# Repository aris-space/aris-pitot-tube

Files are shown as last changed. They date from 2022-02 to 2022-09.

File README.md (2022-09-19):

# ARIS Pitot Tube 

This pitot tube prototype is designed as an all-in-one plug-and-play system to gather data.  
<p align="center">
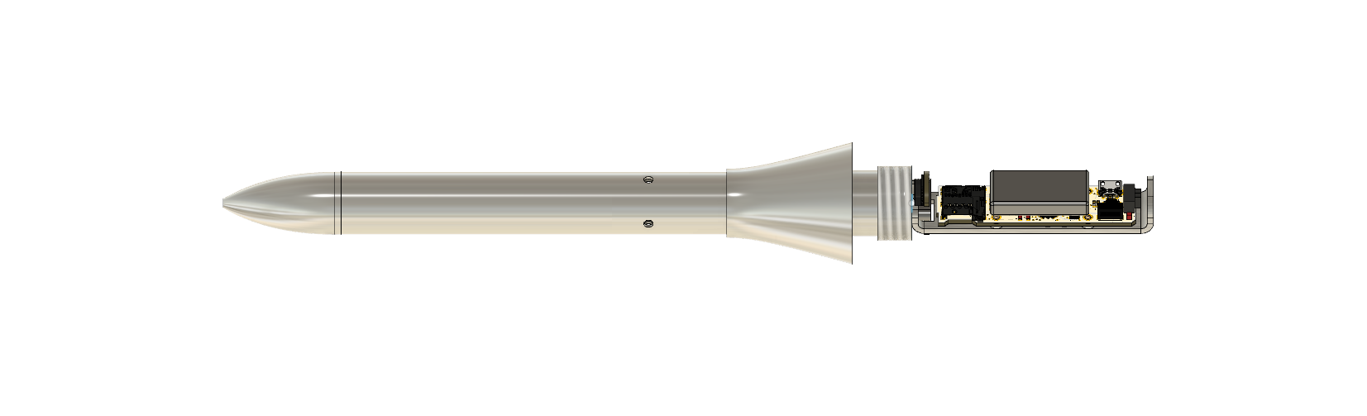
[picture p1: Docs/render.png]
  
</p>
The controller is based on an STM32F405 and mounted directly to the tube along with two MS5803 barometers, one MCP9600 thermocouple ADC, one ICM20601 accelerometer, an SD card and a battery.  
The software uses freeRTOS and will put the MCU in standby mode until the IMU wakes it up during lift-off (interrupt out of IMU to wakeup pin 1 on MCU).  
Preliminary measurements show that the current consumption in flight mode is 150mA and in sleep mode 3mA. With a 240mAh battery, this allows for 80h of sleep time or 1.6h of flight time.  

Below is a diagram explaining the software architecture.  
<p align="center">
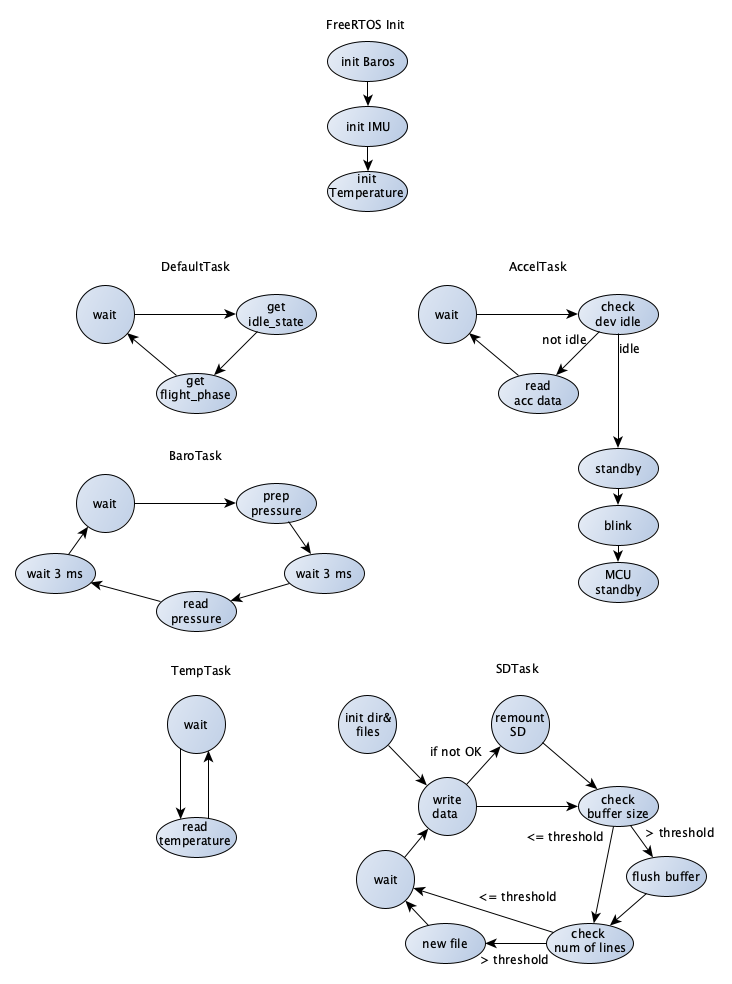
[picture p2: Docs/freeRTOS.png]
  
</p>
  
Repo structure:  
`Hardware` contains all step files and technical drawings to manufacture and assemble the structural components as well as the EAGLE files of the electronics hardware  
`Core/Inc` contains headers of project specific code  
`Core/Src` contains source of project specific code  
`Python` contains python code for analysis (including supersonic flight data from SPAC2022, HELVETIA)  
<p align="center">
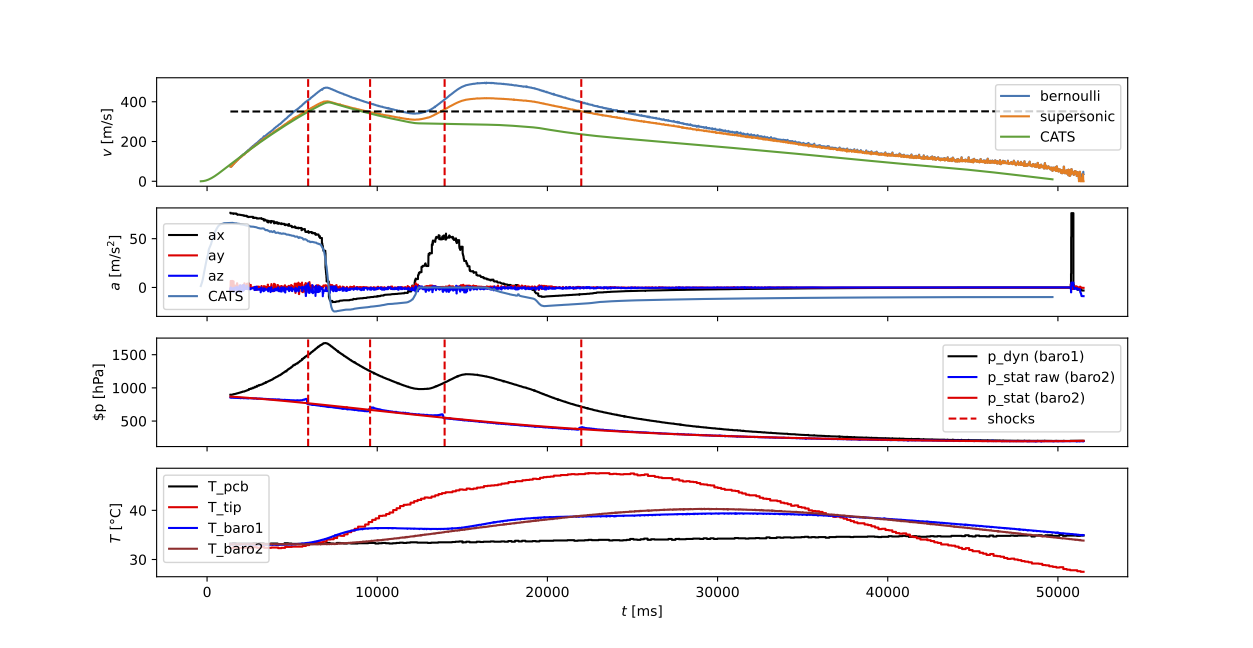
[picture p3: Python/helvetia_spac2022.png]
  
</p>

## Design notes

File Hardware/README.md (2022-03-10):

The CAD with step files and technical drawings can be found in the `CAD` folder.  
`PCB/PitotCTRLBoard` is the controller PCB with the MCU, IMU, ADC and SD-card on it  
`PCB/PitotPBoard3` is the sensor board containing the two Barometers  
The two boards are connected with 3V3, GND, and two I2C lines.  
Consult the `BOM.csv` to order the components, and `assembly_instructions.txt` to mount the hardware.  
`TODO.txt` contains a list of possible improvoments for future interations
<p align="center">
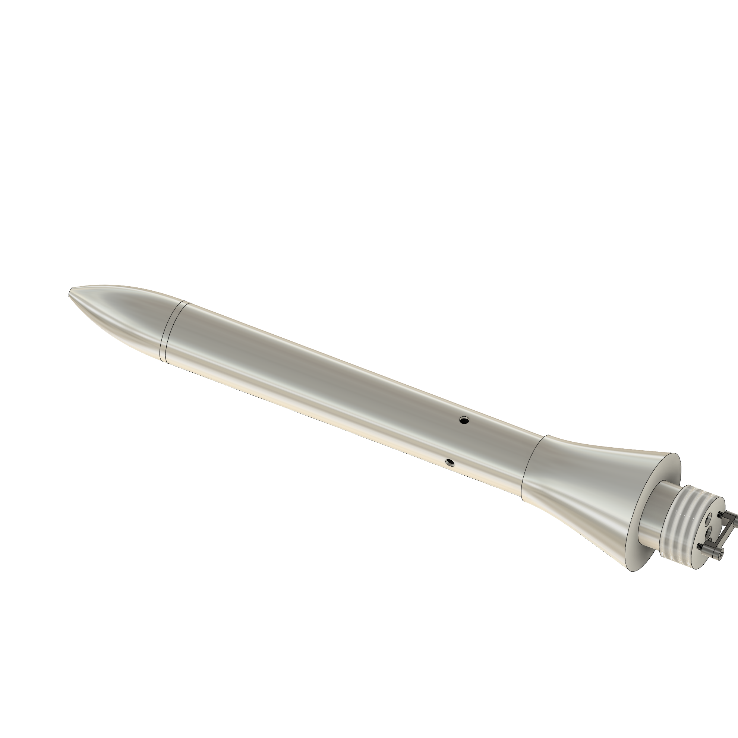
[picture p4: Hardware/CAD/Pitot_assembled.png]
  
</p>

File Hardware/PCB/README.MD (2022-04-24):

`PitotCTRLboard2` is the old control board with micro USB and custom debug connector  

`PitotCTRLboard3` is the new control board with USB-C and Tag-Connect debug connector (PCB is slightly longer)  

`PitotPboard3` is the sensor board, where the barometers are mounted

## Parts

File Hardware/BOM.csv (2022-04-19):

Qty | Value | Device | Package | Parts | Description | ALLIED_NUMBER | ALLIED_PRICE-STOCK | ARROW_PART_NUMBER | ARROW_PRICE-STOCK | AVAILABILITY | CUI_PURCHASE_URL | DESCRIPTION | DIGIKEY-PURCHASE-URL | HEIGHT | MANUFACTURER | MANUFACTURER_NAME | MANUFACTURER_PART_NUMBER | MF | MOUSER-PURCHASE-URL | MOUSER_PART_NUMBER | MOUSER_PRICE-STOCK | MP | PACKAGE | PARTREV | PRICE | RS_PART_NUMBER | RS_PRICE-STOCK | SPICEPREFIX | STANDARD
3 |  | LEDCHIPLED_0805 | CHIPLED_0805 | CHRG / RDY / STAT | LED
12 | 0.1uF | C-EUC0603K | C0603K | C1 / C2 / C3 / C37 | CAPACITOR / European symbol |  |  |  |  |  |  |  |  |  |  |  |  |  |  |  |  |  |  |  |  |  |  | C
1 | 0.47uF | C-EUC0603K | C0603K | C5 | CAPACITOR / European symbol |  |  |  |  |  |  |  |  |  |  |  |  |  |  |  |  |  |  |  |  |  |  | C
6 | 10k | R-EU_R0603 | R0603 | R6 / R7 / R8 / R9 / R12 / R36 | RESISTOR / European symbol |  |  |  |  |  |  |  |  |  |  |  |  |  |  |  |  |  |  |  |  |  |  | R
2 | 15pF | C-EUC0603K | C0603K | C16 / C17 | CAPACITOR / European symbol |  |  |  |  |  |  |  |  |  |  |  |  |  |  |  |  |  |  |  |  |  |  | C
2 | 1k | R-EU_R0603 | R0603 | R43 / R45 | RESISTOR / European symbol |  |  |  |  |  |  |  |  |  |  |  |  |  |  |  |  |  |  |  |  |  |  | R
2 | 1uF | C-EUC0603K | C0603K | C14 / C15 | CAPACITOR / European symbol |  |  |  |  |  |  |  |  |  |  |  |  |  |  |  |  |  |  |  |  |  |  | C
3 | 2.2uF | C-EUC0603K | C0603K | C4 / C11 / C12 | CAPACITOR / European symbol |  |  |  |  |  |  |  |  |  |  |  |  |  |  |  |  |  |  |  |  |  |  | C
1 | 2201778-1 | 2201778-1 | TE_2201778-1 | J1 | MICRO SD PUSH PUSH LOW PROFILE TYPE |  |  |  |  |  |  |  |  |  | TE Connectivity |  |  |  |  |  |  |  |  | B |  |  |  |  | Manufacturer recommendations
1 | 2k | R-EU_R0603 | R0603 | R10 | RESISTOR / European symbol |  |  |  |  |  |  |  |  |  |  |  |  |  |  |  |  |  |  |  |  |  |  | R
1 | 2k2 | R-EU_R0603 | R0603 | R11 | RESISTOR / European symbol |  |  |  |  |  |  |  |  |  |  |  |  |  |  |  |  |  |  |  |  |  |  | R
1 | 330uF | T491C106K035AT | CAPPM6032X280N | C13 | KEMET 10uF 35V dc Tantalum Capacitor MnO2 Solid +/-10% Tolerance T491 Series | 70610893 | https://www.alliedelec.com/kemet-t491c106k035at/70610893/ |  |  |  |  | KEMET 10uF 35V dc Tantalum Capacitor MnO2 Solid +/-10% Tolerance T491 Series |  | 2.8mm |  | Kemet | T491C106K035AT |  |  | 80-T491C106K035 | https://www.mouser.com/Search/Refine.aspx?Keyword=80-T491C106K035 |  |  |  |  | 8015520 | https://uk.rs-online.com/web/p/products/8015520
1 | 3k3 | R-EU_R0603 | R0603 | R13 | RESISTOR / European symbol |  |  |  |  |  |  |  |  |  |  |  |  |  |  |  |  |  |  |  |  |  |  | R
1 | 470 | R-EU_R0603 | R0603 | R14 | RESISTOR / European symbol |  |  |  |  |  |  |  |  |  |  |  |  |  |  |  |  |  |  |  |  |  |  | R
6 | 47k | R-EU_R0603 | R0603 | R1 / R2 / R3 / R4 / R5 / R26 | RESISTOR / European symbol |  |  |  |  |  |  |  |  |  |  |  |  |  |  |  |  |  |  |  |  |  |  | R
1 | ABM8AIG-8.000MHZ-1Z-T | ABM8AIG-8.000MHZ-1Z-T | ABM8AIG8000MHZ1ZT | CLOCK | Crystals 18pF 8MHz 10ppm AEC-Q200 -40C +125C |  |  |  |  |  |  | Crystals 18pF 8MHz 10ppm AEC-Q200 -40C +125C |  | 0.8mm |  | ABRACON | ABM8AIG-8.000MHZ-1Z-T |  |  | 815-M8AIG-8-1ZT | https://www.mouser.com/Search/Refine.aspx?Keyword=815-M8AIG-8-1ZT
1 | BAV16W-7-F | BAV16W-7-F | SOD3716X145N | D5 | Diode Switching 100V 0.15A 2Pin SOD123 Diodes Inc BAV16W-7-F Switching Diode / 300mA 100V / 2-Pin SOD-123 | 70437641 | http://www.alliedelec.com/diodes-inc-bav16w-7-f/70437641/ |  |  |  |  | Diode Switching 100V 0.15A 2Pin SOD123 Diodes Inc BAV16W-7-F Switching Diode / 300mA 100V / 2-Pin SOD-123 |  | 1.45mm |  | Diodes Inc. | BAV16W-7-F |  |  | 621-BAV16W-F | https://www.mouser.com/Search/Refine.aspx?Keyword=621-BAV16W-F |  |  |  |  | 7513430P | http://uk.rs-online.com/web/p/products/7513430P
1 | DEBUG | DEBUG CONNECTOR | DEBUG | U$1 | https://www.mouser.ch/ProductDetail/474-PRT-10361
1 | EG1270 | EG1270 | EG1270 | PWR | E-SWITCH - EG1270 - SWITCH / SLIDE / SPDT / 300mA / 6V / PCB |  |  | EG1270 |  |  |  | E-SWITCH - EG1270 - SWITCH / SLIDE / SPDT / 300mA / 6V / PCB |  | 4.6mm |  | E-Switch | EG1270 |  |  | 612-EG1270 | https://www.mouser.co.uk/ProductDetail/E-Switch/EG1270?qs=xDsBkp9LkodMM2ilVTltow%3D%3D
1 | ICM-20601 | ICM-20601 | PULL-BACK-QFN-16 | ACCEL | IMU ACCEL/GYRO/TEMP I2C/SPI LGA |  |  |  |  |  |  | IMU ACCEL/GYRO/TEMP I2C/SPI LGA |  | mm |  | InvenSense Inc. | ICM-20601 |  |  | 410-ICM-20601 | https://www.mouser.com/Search/Refine.aspx?Keyword=410-ICM-20601
1 | MAX1595EUA33+ | MAX1595EUA33+ | SOP65P490X110-8N | U2 | None |  |  |  |  | Unavailable |  | Charge Pump Switching Regulator IC Positive Fixed 3.3V 1 Output 125mA 8-TSSOP / 8-MSOP (0.118 / 3.00mm Width) |  |  |  |  |  | Maxim Integrated |  |  |  | MAX1595EUA33 | None |  | None
1 | MCP73812 | MCP73831T-2ACI/OT | SOT95P280X145-5N | U$2 | Charge Management Controller Buy Part |  |  |  |  | Warning |  | Charger IC Lithium Ion/Polymer SOT-23-5 | https://snapeda.com/shop?store=DigiKey&id=53208 |  |  |  |  | Microchip | https://snapeda.com/shop?store=Mouser&id=53208 |  |  | MCP73831T-2ACI/OT | SOT-23 Microchip |  | None
1 | MCP9600-E_MX | MCP9600-E_MX | QFN65P500X500X100-21N | TEMP | Board Mount Temperature Sensors Thermocouple to I2C converter |  |  |  |  |  |  | Board Mount Temperature Sensors Thermocouple to I2C converter |  | 1mm |  | Microchip | MCP9600-E/MX |  |  | 579-MCP9600-E/MX | https://www.mouser.com/Search/Refine.aspx?Keyword=579-MCP9600-E%2FMX |  |  |  |  | 1717832P | http://uk.rs-online.com/web/p/products/1717832P
1 | STM32F405RGT6 | STM32F405RGT6 | QFP50P1200X1200X160-64N | U1 | High-performance foundation line / ARM Cortex-M4 core with DSP and FPU / 1 Mbyte Flash / 168 MHz CPU / ART Accelerator |  |  |  |  | Unavailable |  | ARM® Cortex®-M4 STM32F4 Microcontroller IC 32-Bit 168MHz 1MB (1M x 8) FLASH 64-LQFP (10x10) |  |  |  |  |  | STMicroelectronics |  |  |  | STM32F405RGT6 | LQFP-64 STMicroelectronics |  | None
1 | TL3330AF260QG | TL3330AF260QG | TL3330 | RST | Tactile Switches 50mA@12VDC 260g OF Silver contacts |  |  |  |  |  |  | Tactile Switches 50mA@12VDC 260g OF Silver contacts |  | mm |  | E-Switch | TL3330AF260QG |  |  | 612-TL3330AF260QG | https://www.mouser.co.uk/ProductDetail/E-Switch/TL3330AF260QG?qs=cyOInwlKnROnXHK5BnOqnQ%3D%3D
1 | UJ2-MIBH2-4-SMT-TR | UJ2-MIBH2-4-SMT-TR | CUI_UJ2-MIBH2-4-SMT-TR | USB | Micro B Type 5 Pin Horizontal 30 µin Plating SMT USB Jack 2.0 Buy Part |  |  |  |  | Warning | https://www.cuidevices.com/product/interconnect/connectors/usb-connectors/uj2-mibh2-4-smt | Micro B / USB 2.0 / 1.8 A / Right Angle / Surface Mount (SMT) / USB Receptacle | https://snapeda.com/shop?store=DigiKey&id=702231 |  |  |  |  | CUI Devices | https://snapeda.com/shop?store=Mouser&id=702231 |  |  | UJ2-MIBH2-4-SMT-TR | None |  | None
2 | MS580314BA01-00 | MS580314BA01-00 | MS580314BA0100 | IC1 / IC2 | Sensor Pressure SMD MS5803-14BA 14bar | MS580314BA01-00 | https://www.arrow.com/en/products/ms580314ba01-00/te-connectivity | Sensor Pressure SMD MS5803-14BA 14bar | 3.03mm | TE Connectivity | MS580314BA01-00 | 824-MS580314BA01-00 | https://www.mouser.co.uk/ProductDetail/Measurement-Specialties/MS580314BA01-00?qs=oFx6pF86PmChyzStAtLLQA%3D%3D
1 | K-Type | Thermocouple |  |  | at least 30cm of insulated wires
1 | 3.7V Lipo | Battery |  |  | https://www.conrad.ch/de/p/renata-icp521630pm-spezial-akku-prismatisch-kabel-lipo-3-7-v-250-mah-252028.html

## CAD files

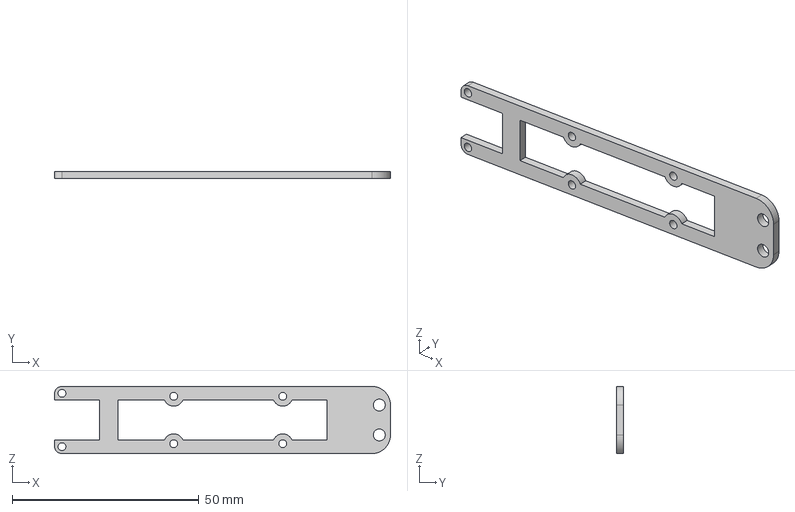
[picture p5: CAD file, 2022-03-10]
Hardware/CAD/Hardware_Order/Sheet_metal/P06_pitot_rack_Abwicklung.step
90.0 x 2.00 x 18.0 mm

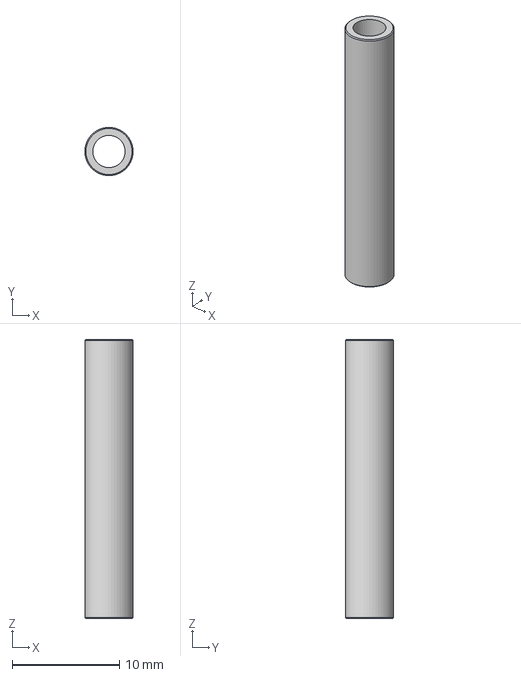
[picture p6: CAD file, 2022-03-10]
Hardware/CAD/Hardware_Order/Solid_parts/P04b_inner_tube.step
4.50 x 4.50 x 26.0 mm

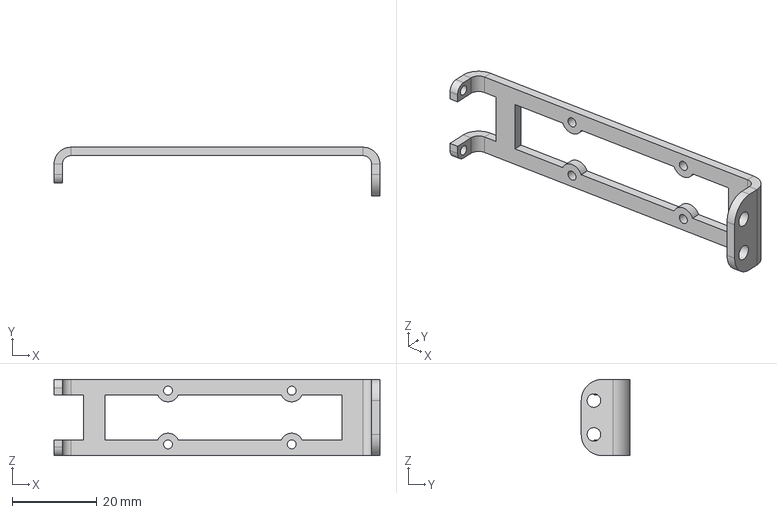
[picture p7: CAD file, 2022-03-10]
Hardware/CAD/Hardware_Order/Sheet_metal/P06_pitot_rack.step
77.0 x 11.5 x 18.0 mm

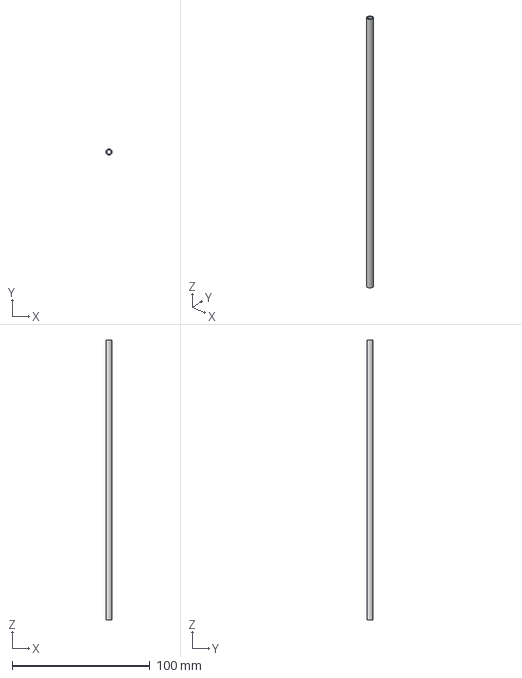
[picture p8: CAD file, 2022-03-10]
Hardware/CAD/Hardware_Order/Solid_parts/P04a_inner_tube.step
4.50 x 4.50 x 203.0 mm

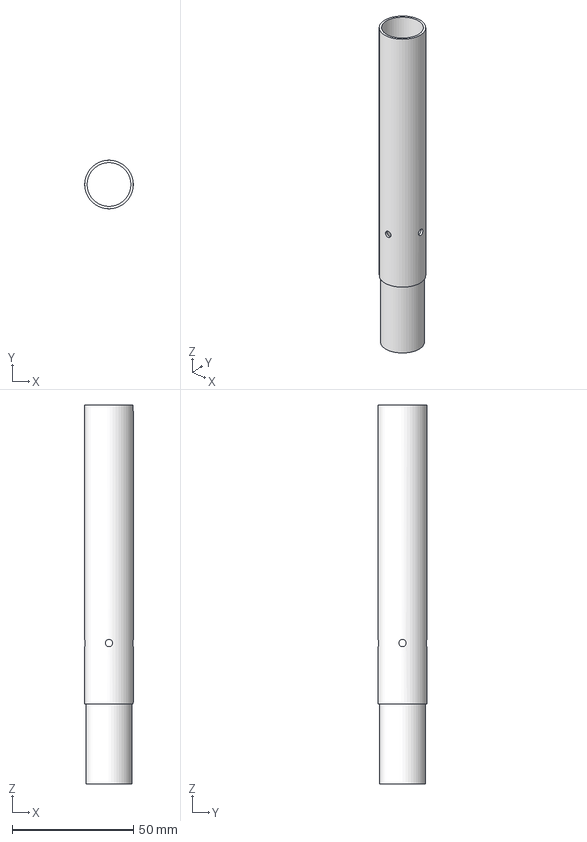
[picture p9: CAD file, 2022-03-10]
Hardware/CAD/Hardware_Order/Solid_parts/P05_outer_tube.step
20.0 x 20.0 x 156.0 mm

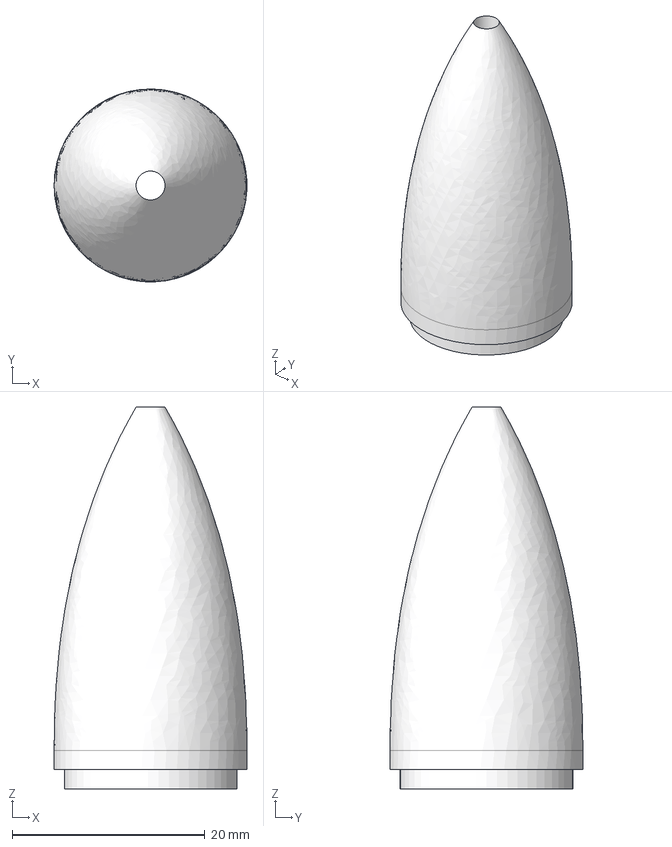
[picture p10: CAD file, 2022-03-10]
Hardware/CAD/Hardware_Order/Solid_parts/P02_tip.step
20.0 x 20.0 x 39.6 mm

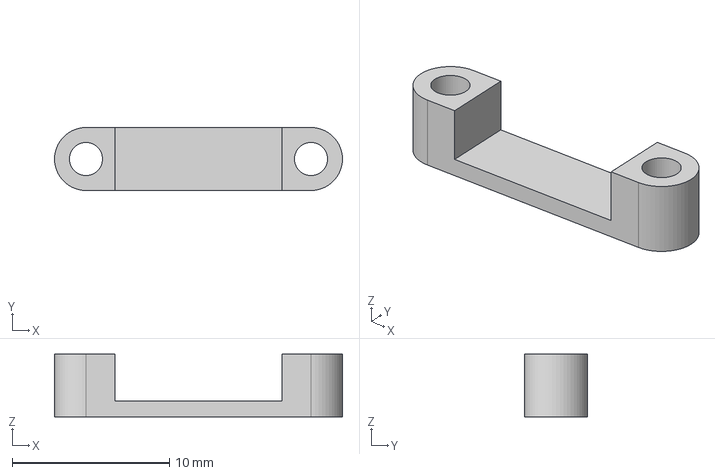
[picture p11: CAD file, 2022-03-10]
Hardware/CAD/Hardware_Order/Solid_parts/P03_sensor_mount.step
18.3 x 4.00 x 4.00 mm

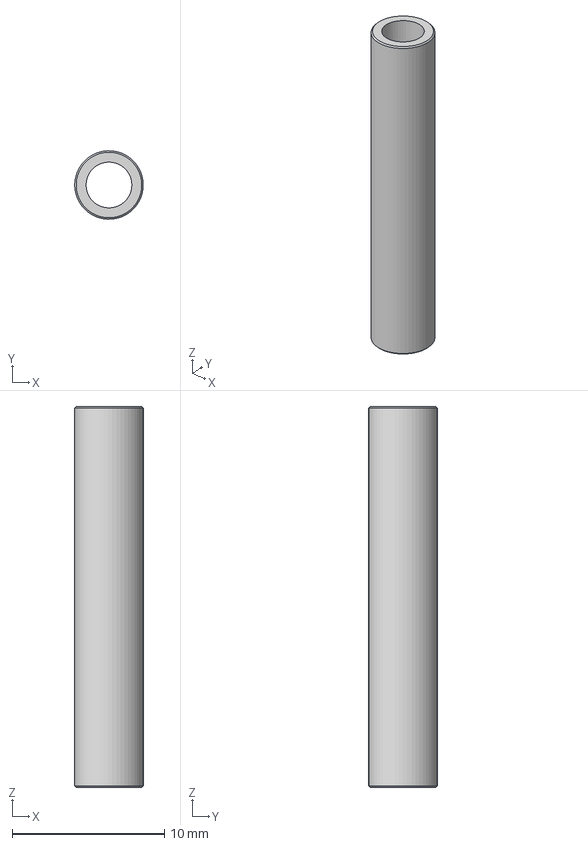
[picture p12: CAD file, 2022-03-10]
Hardware/CAD/Hardware_Order/Solid_parts/P04c_inner_tube.step
4.50 x 4.50 x 25.0 mm

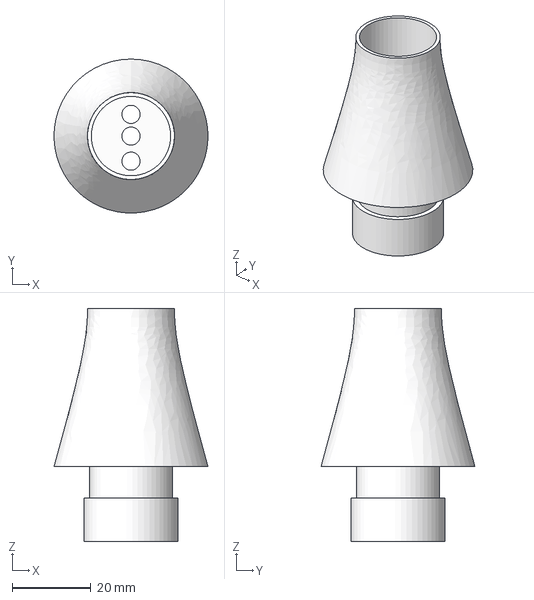
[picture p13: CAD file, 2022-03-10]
Hardware/CAD/Hardware_Order/Solid_parts/P01_screw_mount.step
39.0 x 39.0 x 59.0 mm

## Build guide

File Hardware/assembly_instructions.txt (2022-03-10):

Assembly instructions:
- test if the thermocouple cable fits through the smaller diameter of the guiding tube (we left it out and filled the hole with play-doh)
- glue the tubes into the bottom mount, pay attention that it is straight!
- put the so far assembled part on the lathe and turn down the bottom mount until the transition to the tube is smooth
- guide the thermocouple cable through the bottom mount and tubes
- glue the K-Type thermocouple into the tip
- glue the tip on top of the tubes
- mount the barometer-sensor PCB (clamp it down with the holder-part) to the bottom mount and seal everythign with play-doh (pay attention not to put play-doh on the sensor membranes)
- remove (with a saw) the bottom tab of the rack, it is not needed and in the way of the switch. This was only used in a previous version, you could also adapt the CAD model before ordering
- screw the control PCB on to the rack and mount it to the bottom part
- tape the battery around the control PCB

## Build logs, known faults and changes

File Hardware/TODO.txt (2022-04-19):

TODO for next hardware iteration (order: relevance):
- [Structure] static ports further away from screw-mount but also not too close to the tip
- [Electronics] change the DEBUG connector to something better (e.g. Tag-Connect)
- [Electronics] try to fit a USB-C onto the PCB connector, because cool.
- [Electronics] implement a flash storage chip, to increase sample rate
- [Electronics] consider changing the type of pressure sensor (smaller range, better resolution)
- [Structure] improve the connection of pressure sensor to the metal parts
- [Electronics] implement inter-rocket-wifi/bluetooth to connect to avionics

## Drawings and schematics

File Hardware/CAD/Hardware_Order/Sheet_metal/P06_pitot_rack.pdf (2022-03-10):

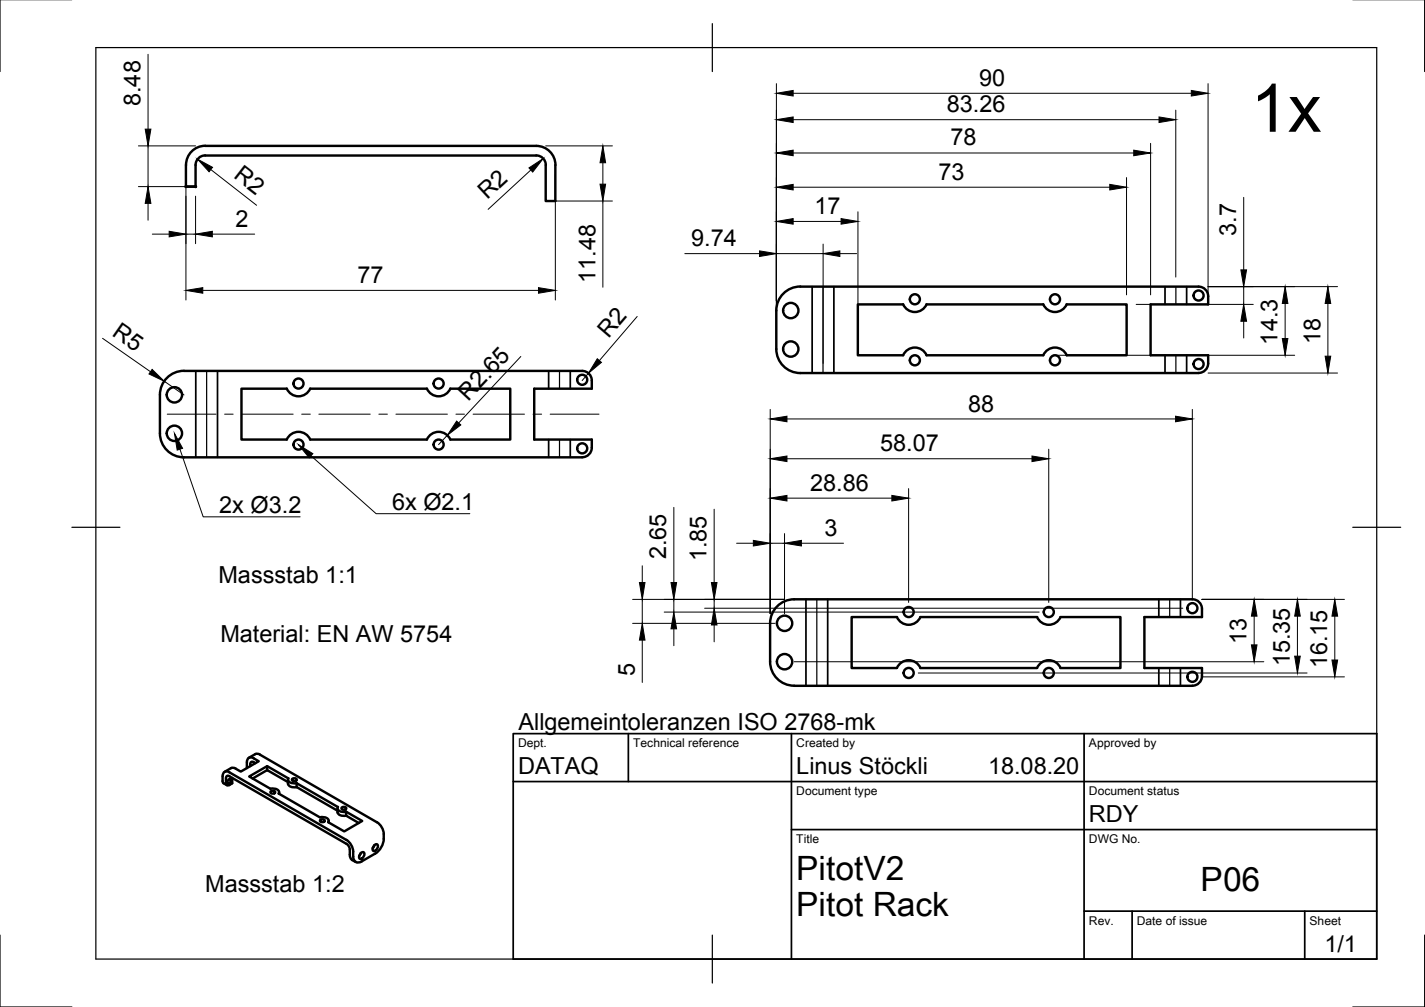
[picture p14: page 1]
DATAQ; Linus Stöckli; Massstab 1:1; Massstab 1:2

Material: EN AW 5754

Allgemeintoleranzen ISO 2768-mk

Dept. | Technical reference | Created by 18.08.20 | Approved by

Document type | Document status RDY

Title Pitot Rack | DWG No. P06 PitotV2

Rev. | Date of issue | Sheet 1/1

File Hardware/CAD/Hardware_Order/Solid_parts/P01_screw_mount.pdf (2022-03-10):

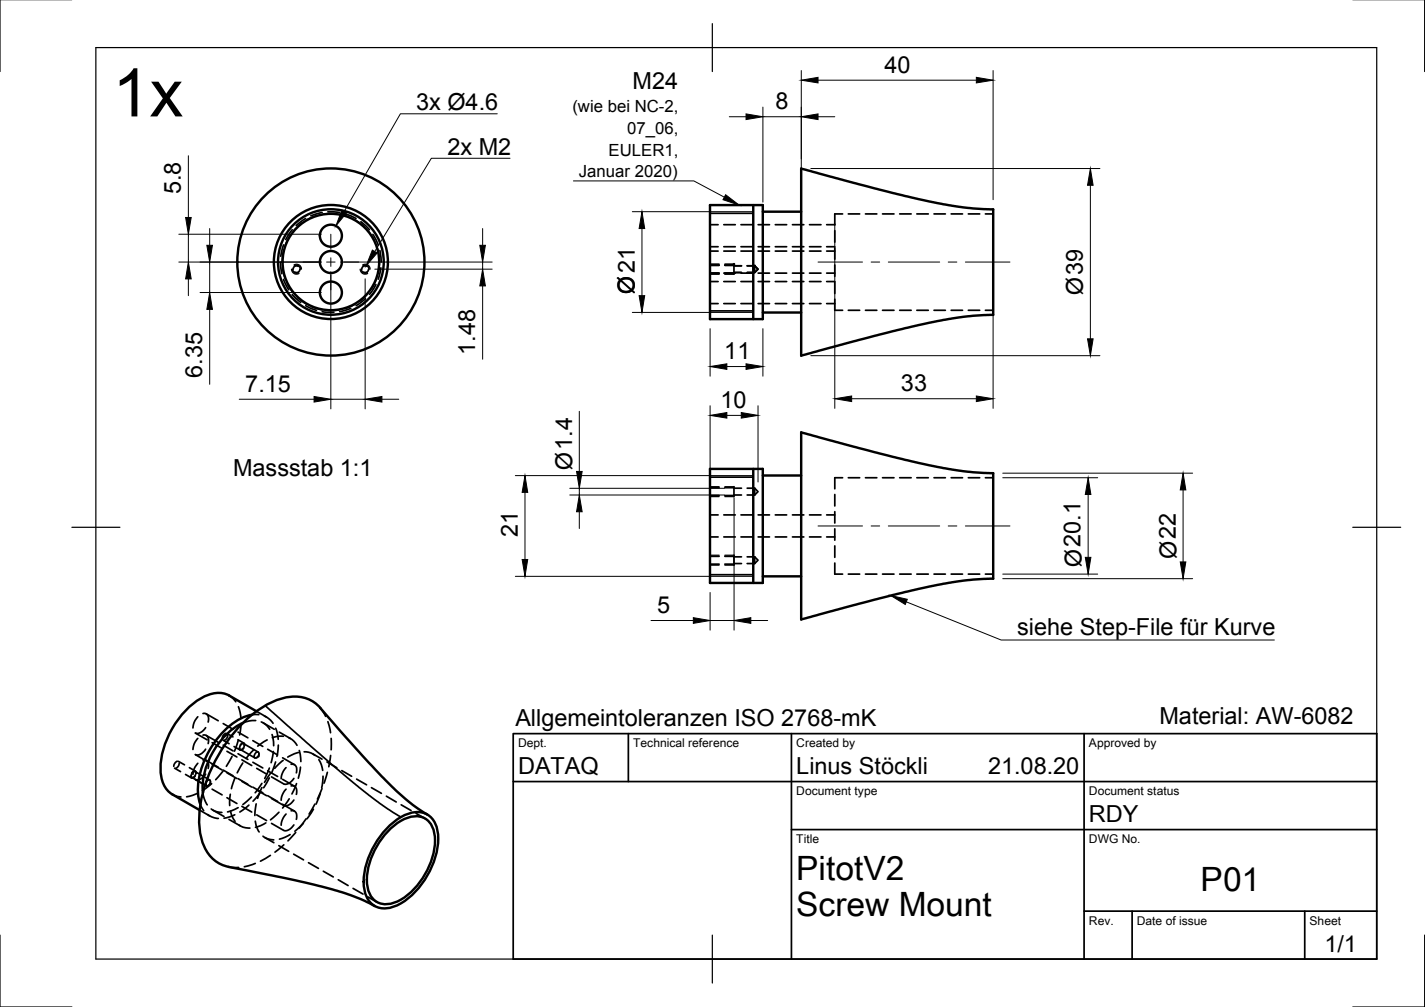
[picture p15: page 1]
Massstab 1:1; Allgemeintoleranzen ISO 2768-mK; Material: AW-6082; Januar 2020)

(wie bei NC-2,

siehe Step-File für Kurve

Dept. DATAQ | Technical reference | Created by Linus Stöckli 21.08.20 | Approved by

Document type | Document status RDY

Title Screw Mount | DWG No. P01 PitotV2

Rev. | Date of issue | Sheet 1/1

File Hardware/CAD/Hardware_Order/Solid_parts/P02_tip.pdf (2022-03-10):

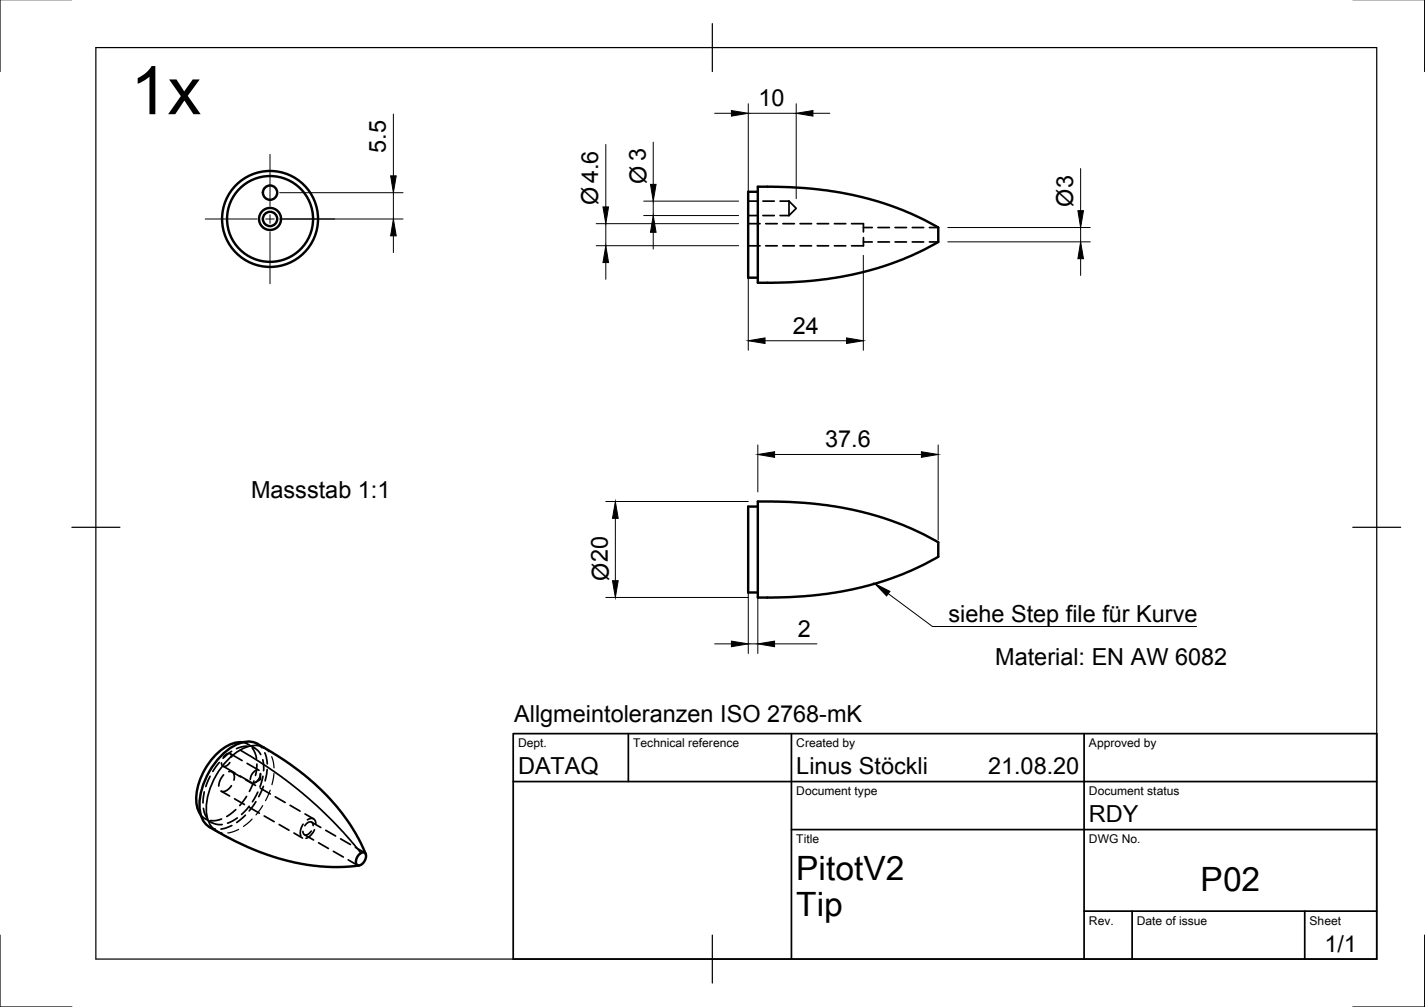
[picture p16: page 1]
DATAQ; Linus Stöckli 4.6; Massstab 1:1

siehe Step file für Kurve 5.5

Material: EN AW 6082

Allgmeintoleranzen ISO 2768-mK

Dept. | Technical reference | Created by 21.08.20 | Approved by

Document type | Document status RDY

Title Tip | DWG No. P02 PitotV2

Rev. | Date of issue | Sheet 1/1

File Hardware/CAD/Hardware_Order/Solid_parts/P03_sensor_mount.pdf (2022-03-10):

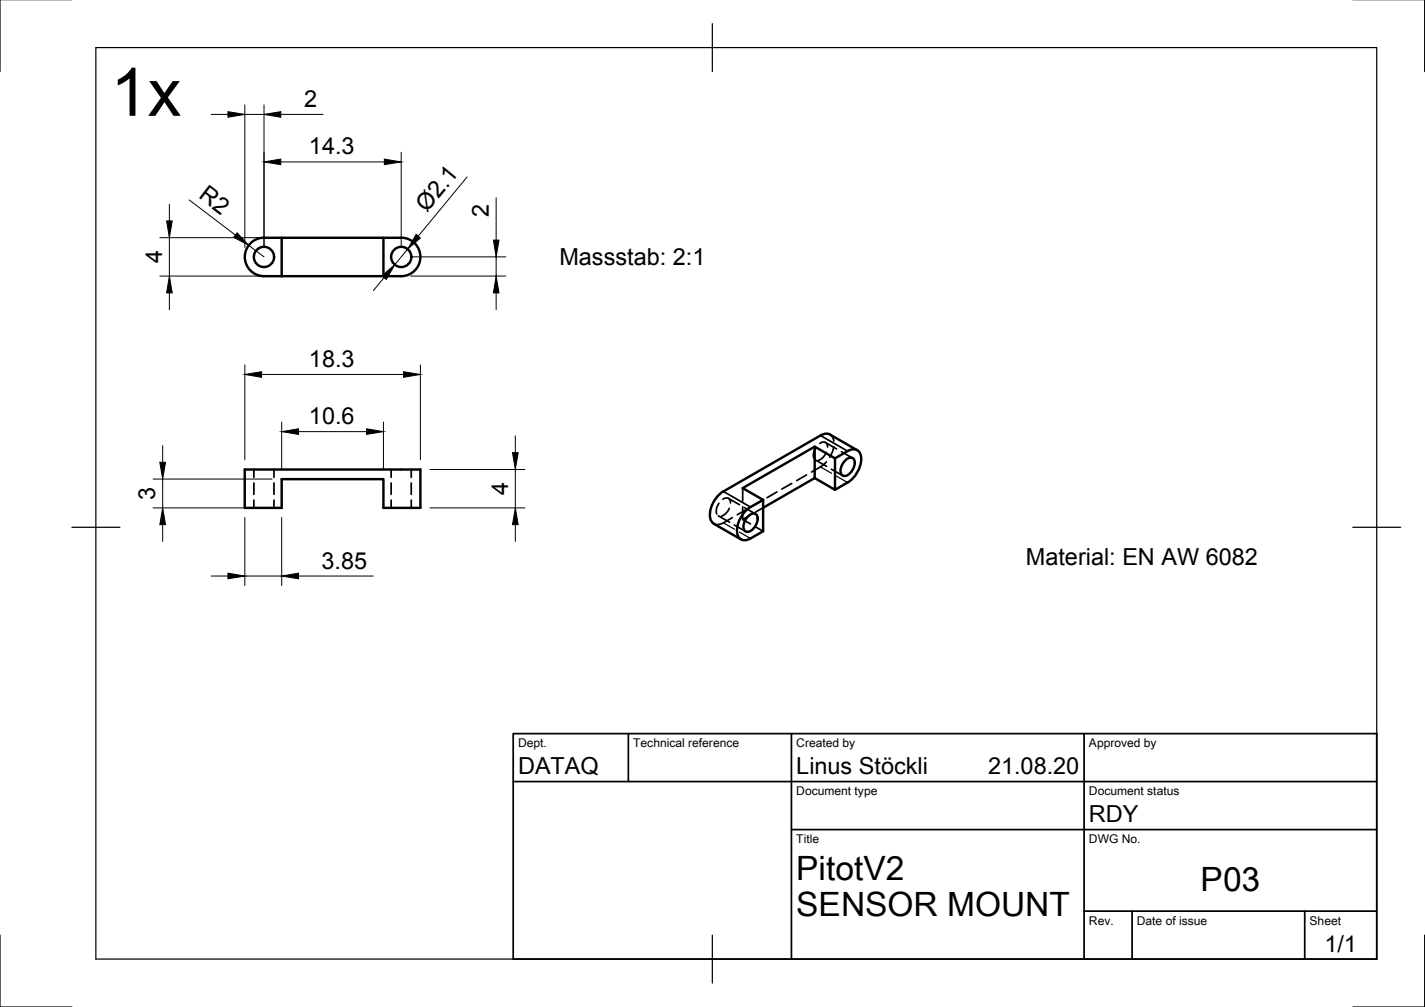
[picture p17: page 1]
Massstab: 2:1

Material: EN AW 6082

Dept. DATAQ | Technical reference | Created by Linus Stöckli 21.08.20 | Approved by

Document type | Document status RDY

Title SENSOR MOUNT | DWG No. P03 PitotV2

Rev. | Date of issue | Sheet 1/1

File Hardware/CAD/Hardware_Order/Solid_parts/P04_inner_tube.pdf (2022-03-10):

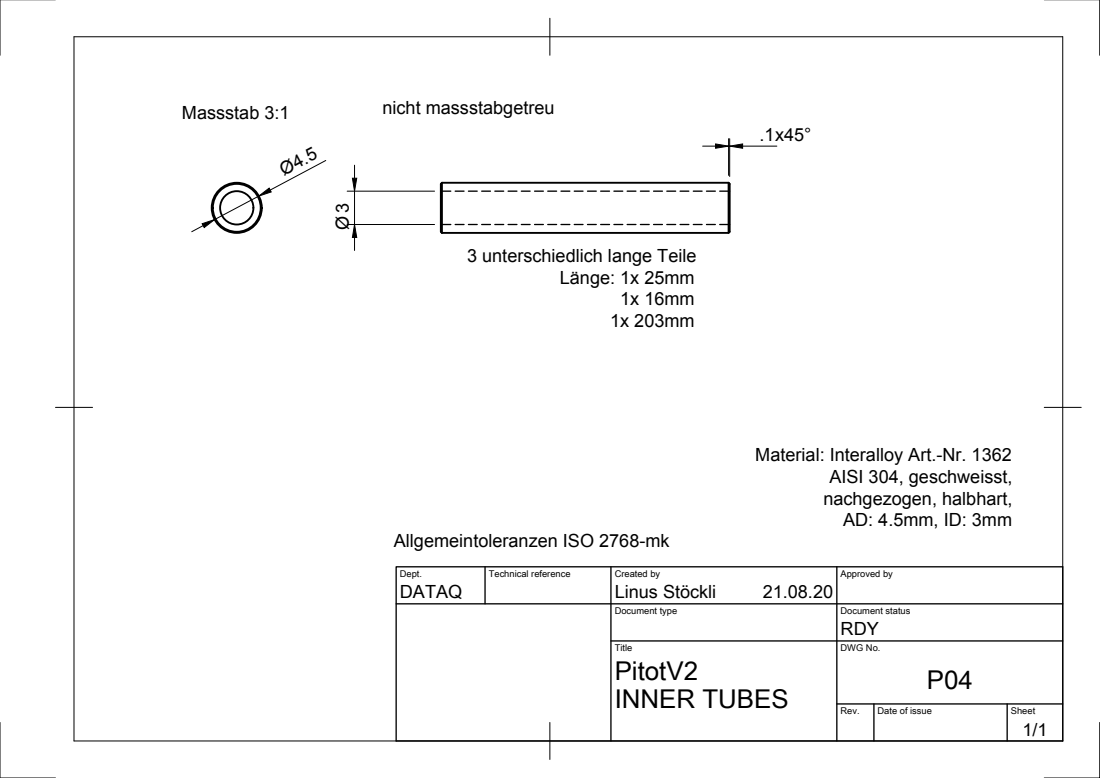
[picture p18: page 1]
Länge: 1x 25mm 1x 16mm 1x 203mm; Massstab 3:1; AISI 304, geschweisst, nachgezogen, halbhart, AD: 4.5mm, ID: 3mm; nicht massstabgetreu

3 unterschiedlich lange Teile

Material: Interalloy Art.-Nr. 1362

Allgemeintoleranzen ISO 2768-mk

Dept. DATAQ | Technical reference | Created by Linus Stöckli 21.08.20 | Approved by

Document type | Document status RDY

Title INNER TUBES | DWG No. P04 PitotV2

Rev. | Date of issue | Sheet 1/1

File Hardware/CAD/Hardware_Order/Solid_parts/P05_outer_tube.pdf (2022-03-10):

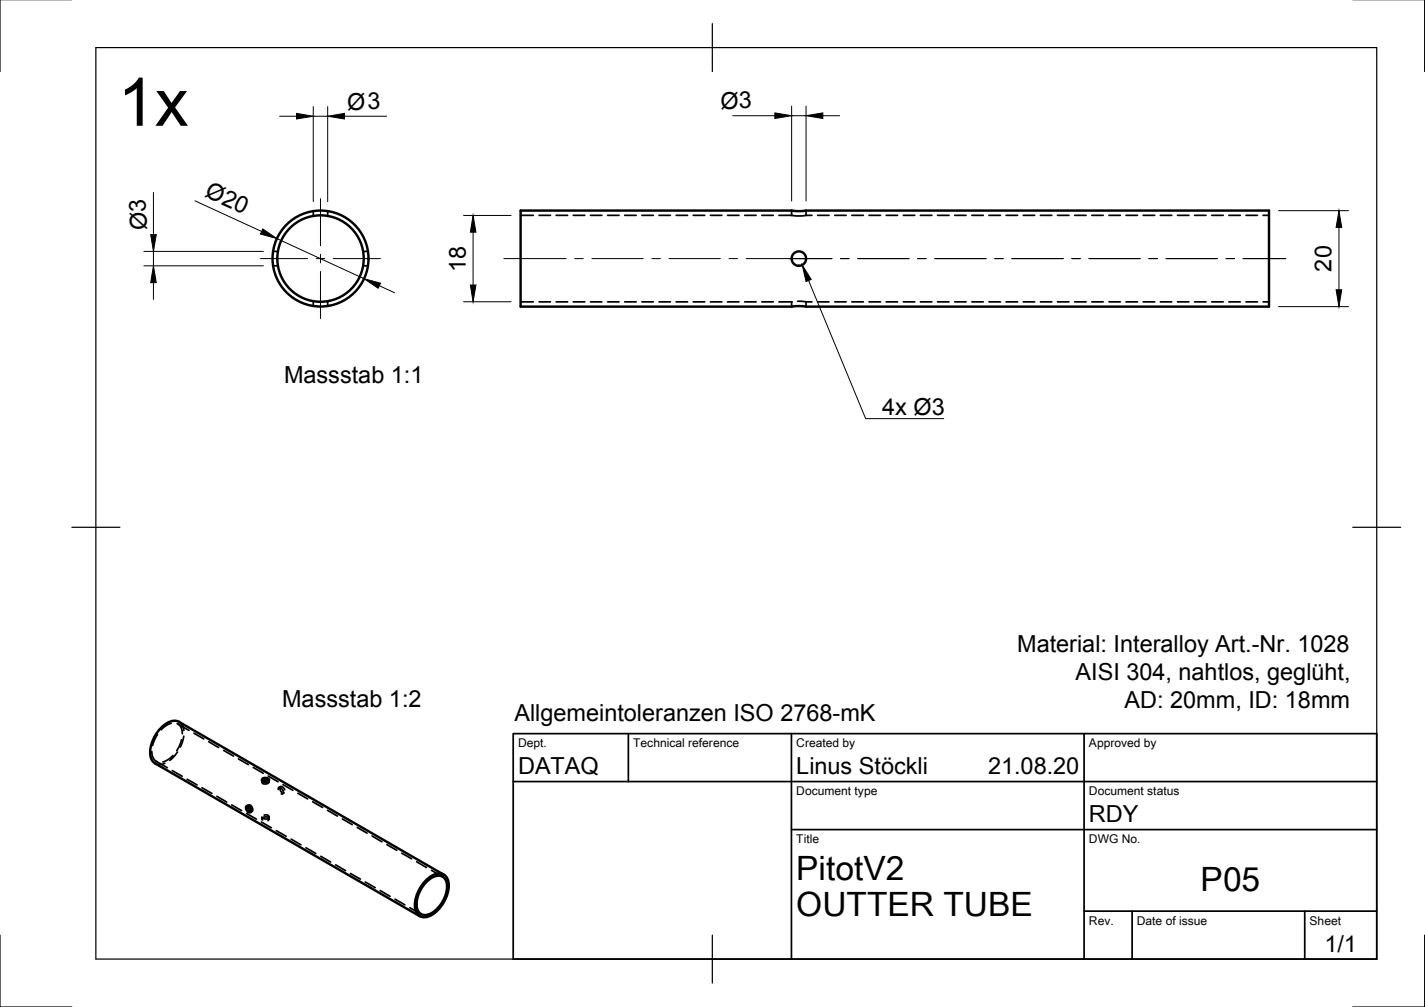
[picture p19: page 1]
Massstab 1:1; Massstab 1:2

Material: Interalloy Art.-Nr. 1028
AISI 304, nahtlos, geglüht,

Allgemeintoleranzen ISO 2768-mK

Dept. DATAQ | Technical reference | Created by Linus Stöckli 21.08.20 | Approved by

Document type | Document status RDY

Title OUTTER TUBE | DWG No. P05 PitotV2

Rev. | Date of issue | Sheet 1/1

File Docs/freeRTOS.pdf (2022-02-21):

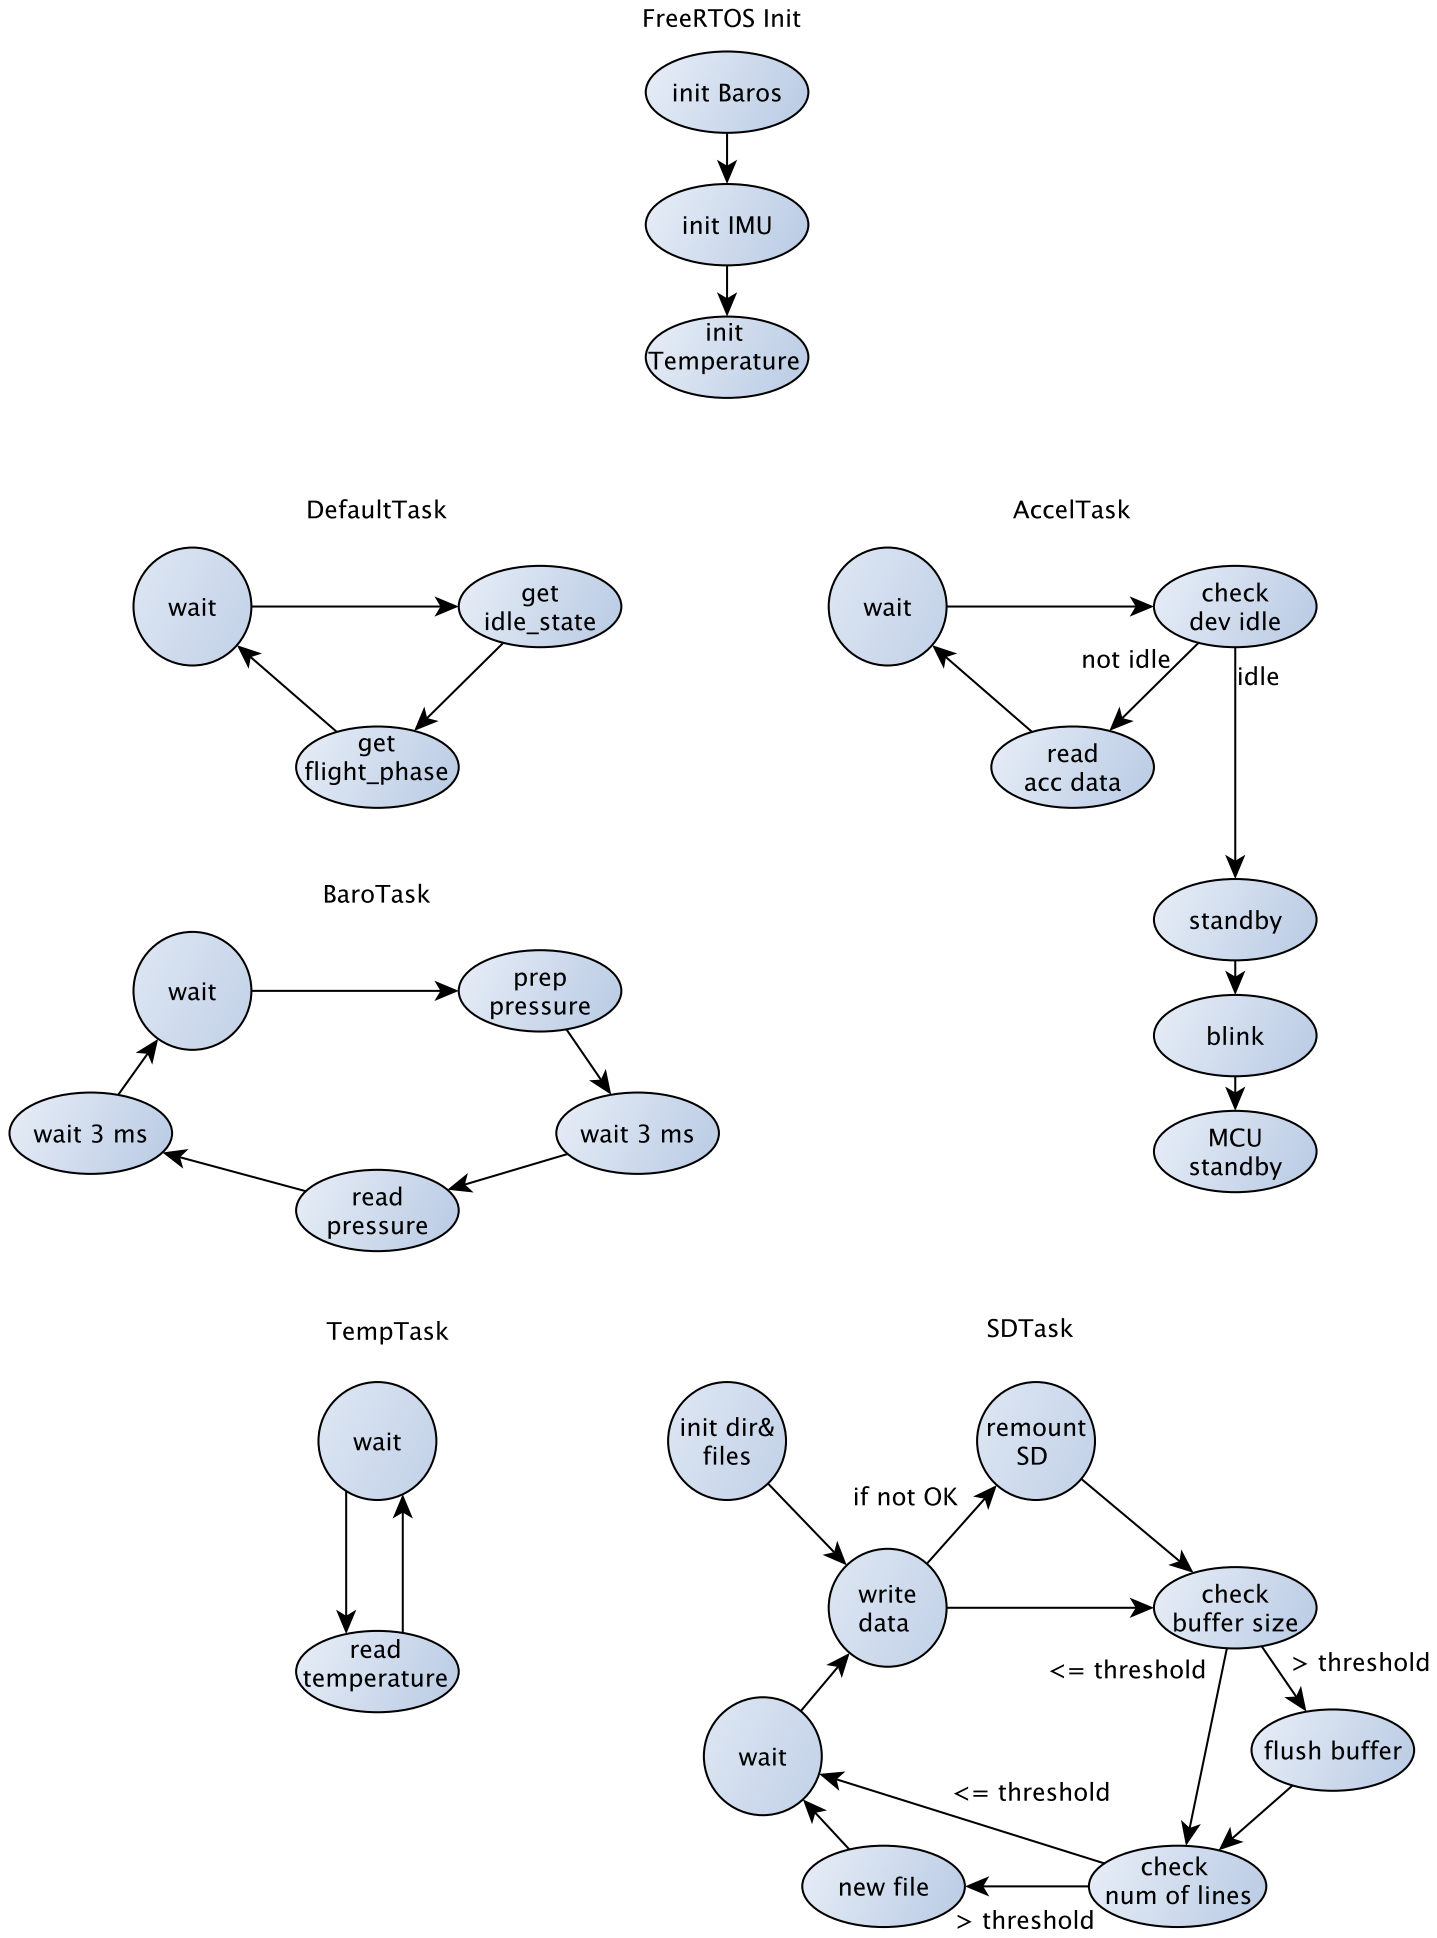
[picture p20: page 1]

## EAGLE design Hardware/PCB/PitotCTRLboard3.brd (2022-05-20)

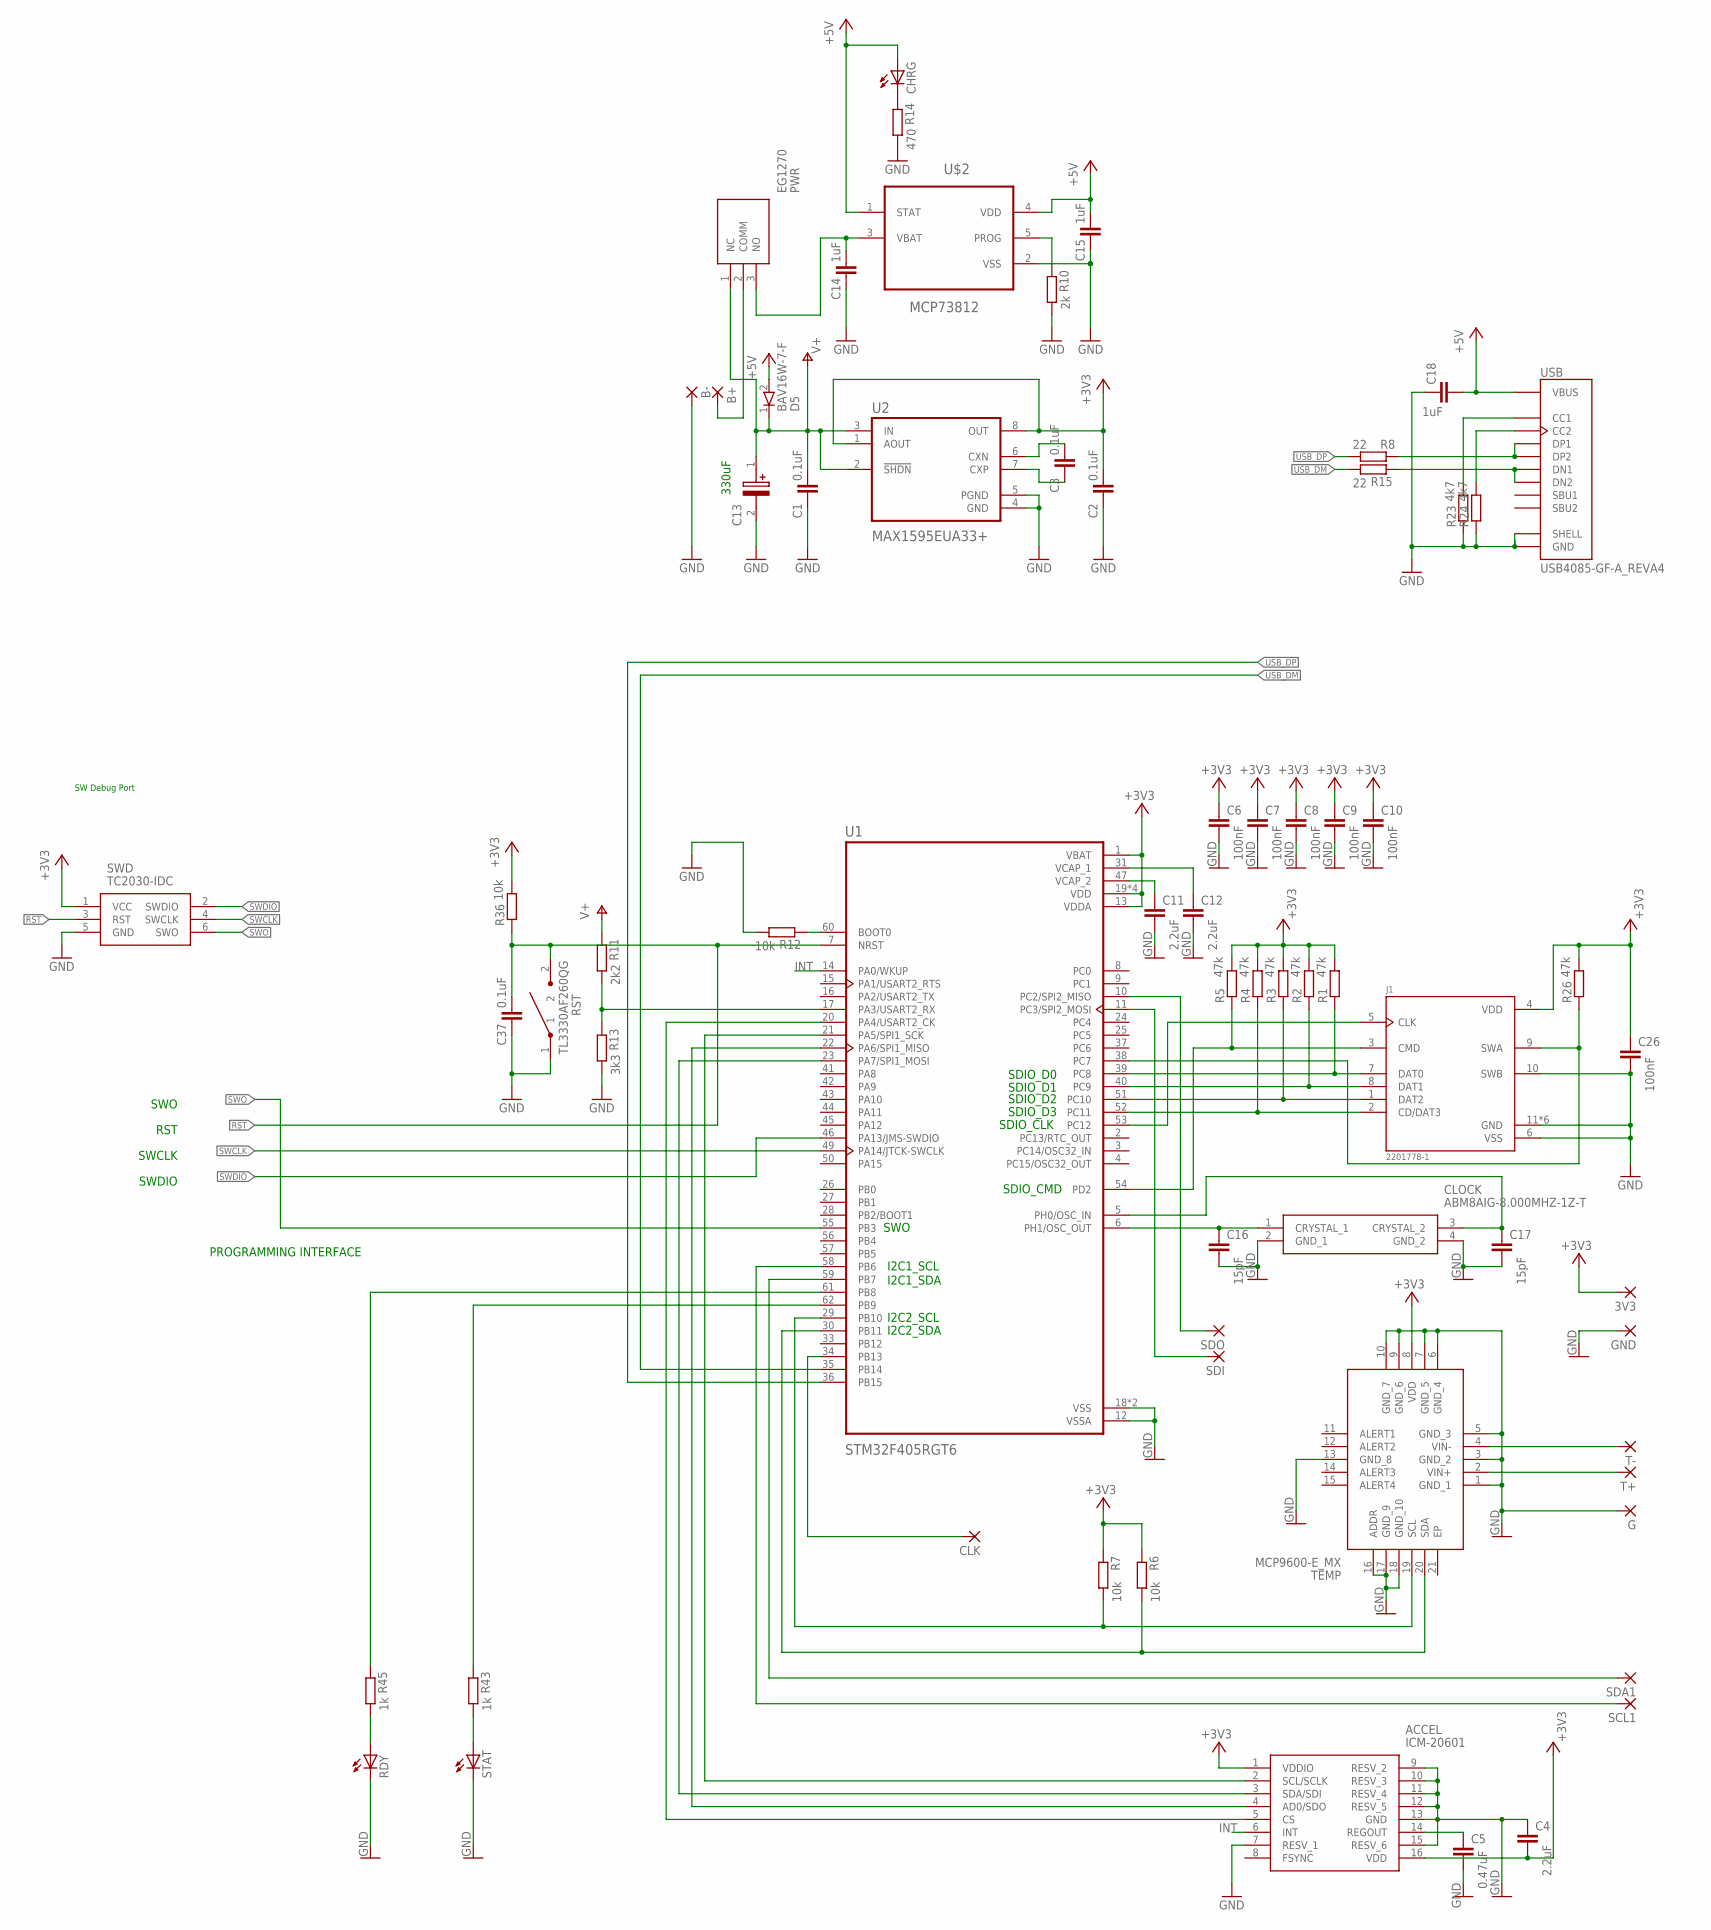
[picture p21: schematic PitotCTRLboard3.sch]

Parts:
3V3: SMD2; SMD1,27-2,54
ACCEL: ICM-20601; PULL-BACK-QFN-16
B+: 1,6/0,9
B-: 1,6/0,9
C1, C2, C3, C37: 0.1uF; C0603K
C4, C11, C12: 2.2uF; C0603K
C5: 0.47uF; C0603K
C6, C7, C8, C9, C10, C26: 100nF; C0603K
C13: 330uF; CAPPM6032X280N
C14, C15, C18: 1uF; C0603K
C16, C17: 15pF; C0603K
CHRG: LEDCHIPLED_0805; CHIPLED_0805
CLK: SMD2; SMD1,27-2,54
CLOCK: ABM8AIG-8.000MHZ-1Z-T; ABM8AIG8000MHZ1ZT
D5: BAV16W-7-F; SOD3716X145N
G: 1,6/0,9
GND: SMD2; SMD1,27-2,54
J1: 2201778-1; TE_2201778-1
PWR: EG1270
R1, R2, R3, R4, R5, R26: 47k; R0603
R6, R7, R12, R36: 10k; R0603
R8, R15: 22; R0603
R10: 2k; R0603
R11: 2k2; R0603
R13: 3k3; R0603
R14: 470; R0603
R23, R24: 4k7; R0603
R43, R45: 1k; R0603
RDY: LEDCHIPLED_0805; CHIPLED_0805
RST: TL3330AF260QG; TL3330
SCL1: SMD2; SMD1,27-2,54
SDA1: SMD2; SMD1,27-2,54
SDI: SMD2; SMD1,27-2,54
SDO: SMD2; SMD1,27-2,54
STAT: LEDCHIPLED_0805; CHIPLED_0805
SWD: TC2030-IDC; TC2030IDC
T+: 1,6/0,9
T-: 1,6/0,9
TEMP: MCP9600-E_MX; QFN65P500X500X100-21N
U1: STM32F405RGT6; QFP50P1200X1200X160-64N
U2: MAX1595EUA33+; SOP65P490X110-8N
U$2: MCP73812; SOT95P280X145-5N
USB: USB4085-GF-A_REVA4; GCT_USB4085-GF-A_REVA4

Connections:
+3V3: 3V3.1, ACCEL.1 (VDDIO), ACCEL.16 (VDD), C2.1, C4.2, C6.1, C7.1, C8.1, C9.1, C10.1, C26.1, J1.4 (VDD), R1.2, R2.2, R3.2, R4.2, R5.2, R6.1, R7.1, R26.2, R36.2, SWD.1 (VCC), TEMP.8 (VDD), U1.1 (VBAT), U1.13 (VDDA), U1.19 (VDD), U1.32 (VDD), U1.48 (VDD), U1.64 (VDD), U2.1 (AOUT), U2.8 (OUT)
+5V: C15.1, C18.2, CHRG.A, D5.2 (A), U$2.1 (STAT), U$2.4 (VDD), USB.A4 (VBUS), USB.A9 (VBUS), USB.B4 (VBUS), USB.B9 (VBUS)
GND: ACCEL.7 (RESV_1), ACCEL.9 (RESV_2), ACCEL.10 (RESV_3), ACCEL.11 (RESV_4), ACCEL.12 (RESV_5), ACCEL.13 (GND), ACCEL.15 (RESV_6), B-.1, C1.2, C2.2, C4.1, C5.2, C6.2, C7.2, C8.2, C9.2, C10.2, C11.2, C12.2, C13.2 (-), C14.2, C15.2, C16.2, C17.2, C18.1, C26.2, C37.2, CLOCK.2 (GND_1), CLOCK.4 (GND_2), G.1, GND.1, J1.6 (VSS), J1.10 (SWB), J1.11 (GND), J1.12 (GND), J1.13 (GND), J1.14 (GND), J1.15 (GND), J1.16 (GND), R10.2, R12.2, R13.2, R14.2, R23.1, R24.1, RDY.C, RST.1, STAT.C, SWD.5 (GND), TEMP.1 (GND_1), TEMP.3 (GND_2), TEMP.5 (GND_3), TEMP.6 (GND_4), TEMP.7 (GND_5), TEMP.9 (GND_6), TEMP.10 (GND_7), TEMP.13 (GND_8), TEMP.16 (ADDR), TEMP.17 (GND_9), TEMP.18 (GND_10), U1.12 (VSSA), U1.18 (VSS), U1.63 (VSS), U2.4 (GND), U2.5 (PGND), U$2.2 (VSS), USB.A1 (GND), USB.A12 (GND), USB.B1 (GND), USB.B12 (GND), USB.P1 (SHELL), USB.P2 (SHELL), USB.P3 (SHELL), USB.P4 (SHELL)
INT: ACCEL.6 (INT), U1.14 (PA0/WKUP)
unnamed: T-.1, TEMP.4 (VIN-)
unnamed: T+.1, TEMP.2 (VIN+)
unnamed: SDA1.1, U1.59 (PB7)
unnamed: SCL1.1, U1.58 (PB6)
unnamed: J1.7 (DAT0), R1.1, U1.39 (PC8)
unnamed: J1.8 (DAT1), R2.1, U1.40 (PC9)
unnamed: J1.1 (DAT2), R3.1, U1.51 (PC10)
unnamed: J1.2 (CD/DAT3), R4.1, U1.52 (PC11)
unnamed: J1.3 (CMD), R5.1, U1.54 (PD2)
unnamed: R7.2, TEMP.19 (SCL), U1.29 (PB10)
unnamed: R6.2, TEMP.20 (SDA), U1.30 (PB11)
unnamed: ACCEL.2 (SCL/SCLK), U1.21 (PA5/SPI1_SCK)
unnamed: ACCEL.4 (AD0/SDO), U1.22 (PA6/SPI1_MISO)
unnamed: ACCEL.3 (SDA/SDI), U1.23 (PA7/SPI1_MOSI)
unnamed: ACCEL.5 (CS), U1.20 (PA4/USART2_CK)
unnamed: J1.5 (CLK), U1.53 (PC12)
unnamed: R12.1, U1.60 (BOOT0)
unnamed: R43.2, STAT.A
unnamed: R43.1, U1.62 (PB9)
unnamed: R45.1, U1.61 (PB8)
unnamed: C17.1, CLOCK.3 (CRYSTAL_2), U1.5 (PH0/OSC_IN)
unnamed: B+.1, PWR.2 (COMM)
unnamed: C3.1, U2.6 (CXN)
unnamed: C3.2, U2.7 (CXP)
unnamed: ACCEL.14 (REGOUT), C5.1
unnamed: C12.1, U1.31 (VCAP_1)
unnamed: C11.1, U1.47 (VCAP_2)
unnamed: R10.1, U$2.5 (PROG)
unnamed: R11.2, R13.1, U1.17 (PA3/USART2_RX)
unnamed: C14.1, PWR.3 (NO), U$2.3 (VBAT)
unnamed: C16.1, CLOCK.1 (CRYSTAL_1), U1.6 (PH1/OSC_OUT)
unnamed: R8.1, USB.A6 (DP1), USB.B6 (DP2)
unnamed: CHRG.C, R14.1
unnamed: SDO.1, U1.10 (PC2/SPI2_MISO)
unnamed: SDI.1, U1.11 (PC3/SPI2_MOSI)
unnamed: CLK.1, U1.34 (PB13)
unnamed: R24.2, USB.B5 (CC2)
unnamed: R23.2, USB.A5 (CC1)
unnamed: R45.2, RDY.A
unnamed: R15.1, USB.A7 (DN1), USB.B7 (DN2)
unnamed: J1.9 (SWA), R26.1, U1.38 (PC7)
RST: C37.1, R36.1, RST.2, SWD.3 (RST), U1.7 (NRST)
SWCLK: SWD.4 (SWCLK), U1.49 (PA14/JTCK-SWCLK)
SWDIO: SWD.2 (SWDIO), U1.46 (PA13/JMS-SWDIO)
SWO: SWD.6 (SWO), U1.55 (PB3)
USB_DM: R15.2, U1.35 (PB14)
USB_DP: R8.2, U1.36 (PB15)
V+: C1.1, C13.1 (+), D5.1 (K), PWR.1 (NC), R11.1, U2.2 (!SHDN), U2.3 (IN)

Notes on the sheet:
RST
SWDIO
SWCLK
PROGRAMMING INTERFACE
SWO
I2C2_SCL
I2C2_SDA
I2C1_SCL
I2C1_SDA
SDIO_D2
SDIO_D3
SDIO_CLK
SDIO_D1
SDIO_D0
SDIO_CMD
330uF
SW Debug Port

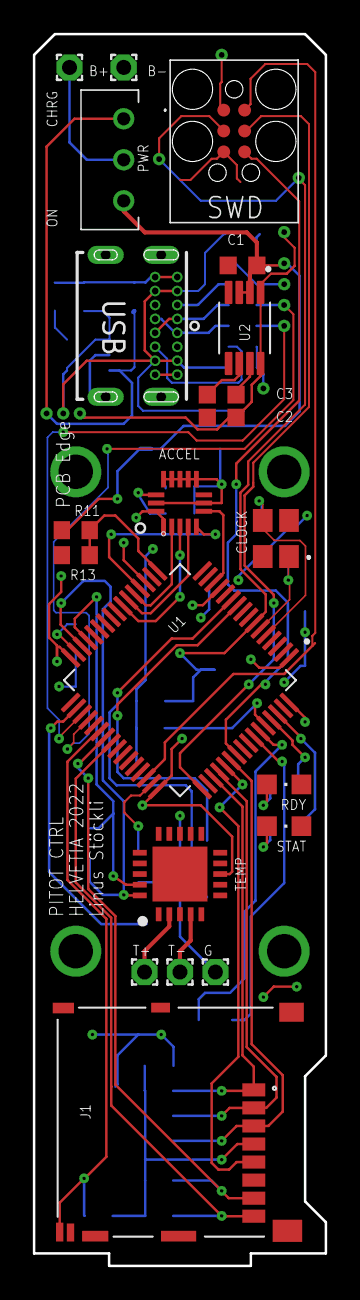
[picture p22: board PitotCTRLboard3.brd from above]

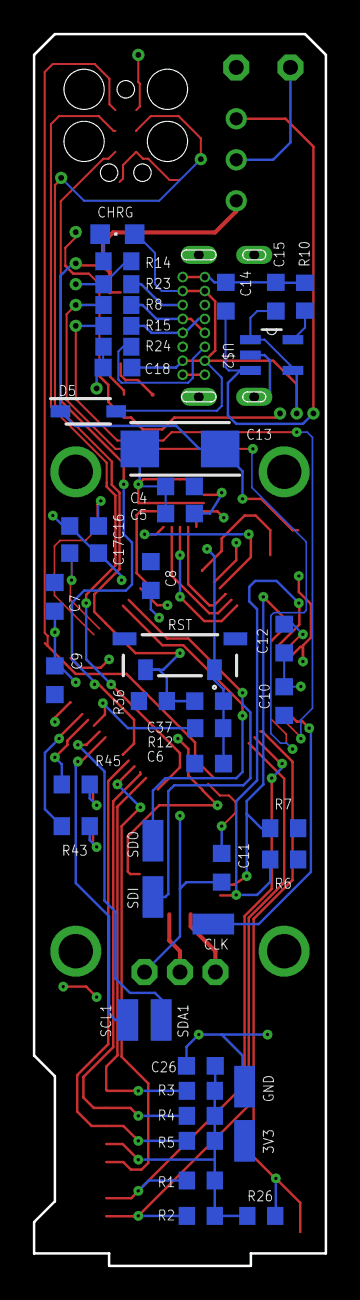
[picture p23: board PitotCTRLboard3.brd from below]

Board: 2 copper layers, 17.8 x 75.1 mm, 67 parts (46 on the bottom side), 52 nets.

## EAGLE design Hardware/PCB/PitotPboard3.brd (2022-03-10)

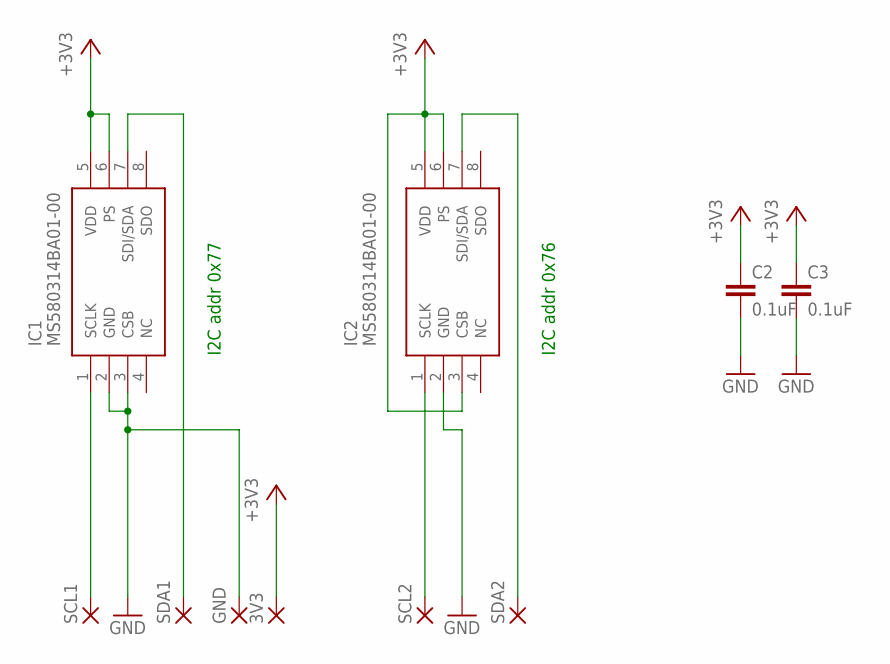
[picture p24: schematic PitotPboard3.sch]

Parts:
3V3: 1,6/0,9
C2, C3: 0.1uF; C0603K
GND: 1,6/0,9
IC1, IC2: MS580314BA01-00; MS580314BA0100
SCL1, SCL2: 1,6/0,9
SDA1, SDA2: 1,6/0,9

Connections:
+3V3: 3V3.1, C2.1, C3.1, IC1.5 (VDD), IC1.6 (PS), IC2.3 (CSB), IC2.5 (VDD), IC2.6 (PS)
GND: C2.2, C3.2, GND.1, IC1.2 (GND), IC1.3 (CSB), IC2.2 (GND)
unnamed: IC2.1 (SCLK), SCL2.1
unnamed: IC2.7 (SDI/SDA), SDA2.1
unnamed: IC1.7 (SDI/SDA), SDA1.1
SCK: IC1.1 (SCLK), SCL1.1

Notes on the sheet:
I2C addr 0x77
I2C addr 0x76

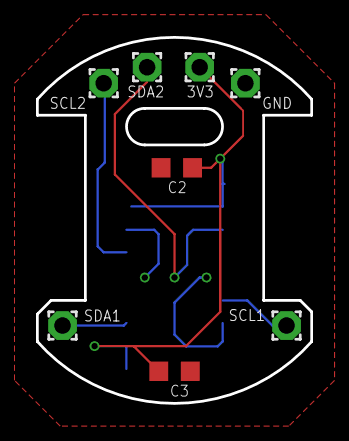
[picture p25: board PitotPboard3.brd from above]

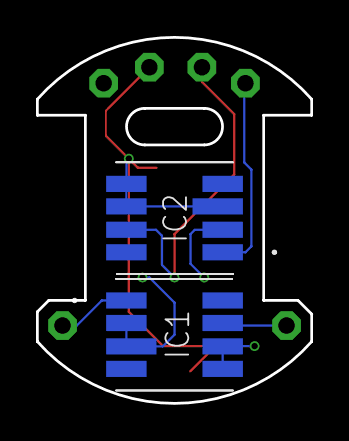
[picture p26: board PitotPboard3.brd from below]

Board: 2 copper layers, 15.2 x 20.3 mm, 10 parts (2 on the bottom side), 6 nets.

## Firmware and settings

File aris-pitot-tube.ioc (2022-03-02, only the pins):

Mcu.UserName=STM32F405RGTx
PA0-WKUP.Signal=SYS_WKUP
PA13.Signal=SYS_JTMS-SWDIO
PA14.Signal=SYS_JTCK-SWCLK
PA4.GPIO_Label=SPI1_CS
PA4.Signal=GPIO_Output
PA5.Signal=SPI1_SCK
PA6.Signal=SPI1_MISO
PA7.Signal=SPI1_MOSI
PB10.Signal=I2C2_SCL
PB11.Signal=I2C2_SDA
PB3.Signal=SYS_JTDO-SWO
PB6.Signal=I2C1_SCL
PB7.Signal=I2C1_SDA
PB8.GPIO_Label=RDY
PB8.Signal=GPIO_Output
PB9.GPIO_Label=STAT
PB9.Signal=GPIO_Output
PC10.Signal=SDIO_D2
PC11.Signal=SDIO_D3
PC12.Signal=SDIO_CK
PC7.Signal=GPIO_Input
PC8.Signal=SDIO_D0
PC9.Signal=SDIO_D1
PD2.Signal=SDIO_CMD
PH0-OSC_IN.Signal=RCC_OSC_IN
PH1-OSC_OUT.Signal=RCC_OSC_OUT

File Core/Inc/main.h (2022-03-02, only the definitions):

#define BUFLEN 128
#define DEBUG_PRINT 0
#define SPI1_CS_Pin GPIO_PIN_4
#define SPI1_CS_GPIO_Port GPIOA
#define RDY_Pin GPIO_PIN_8
#define RDY_GPIO_Port GPIOB
#define STAT_Pin GPIO_PIN_9
#define STAT_GPIO_Port GPIOB

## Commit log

2022-02-07 initial commit ( w/ code)
    tested stop mode and WOM interrupt
2022-02-10 add project files for STM32CubeIDE
2022-02-17 check if sensor response is okay
2022-02-17 sensor response and new SD directories/file format
2022-02-21 added hardware files + software structure graph
    [PitotCTRLboard.brd, PitotCTRLboard.sch]
2022-02-21 implemented gyro in idle detect
2022-02-22 add TODO and debug prints
2022-02-22 include gyro in idle detect
2022-02-22 add render of pitot tube
2022-03-10 added schematics, pcb routing, TODO, BOM and assembly instructions
    [BOM.csv, PitotCTRLboard.brd, PitotPboard3.brd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]
2022-03-10 added CAD
    [P01_screw_mount.step, P02_tip.step, P03_sensor_mount.step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]
2022-03-10 change delimiter
    [BOM.csv]
2022-04-15 add battery to BOM.csv
    [BOM.csv]
2022-04-19 PCB fix
    [PitotCTRLboard2.brd, PitotCTRLboard2.sch]
2022-04-21 add sensor-board gerber files
2022-04-21 add ctrl-board gerber files
2022-04-21 changed text from euler to helvetia
    [PitotCTRLboard2.brd]
2022-04-22 added pitot ctrl board 3 (includes USBC and new debug connector)
    [PitotCTRLboard3.brd, PitotCTRLboard3.sch]
2022-04-22 fix a via under usb-c
    [PitotCTRLboard3.brd]
2022-04-22 fix via
    [PitotCTRLboard3.brd]
2022-04-24 fix usb-c position
    [PitotCTRLboard3.brd]
2022-05-20 bug fix
    [PitotCTRLboard3.brd, PitotCTRLboard3.sch]
2022-09-19 add python files for analysis 📉
    [Helvetia - flight_info_processed.csv, LOG.CSV]
2022-09-19 add plot of HELVETIA@SPAC2022 🇨🇭

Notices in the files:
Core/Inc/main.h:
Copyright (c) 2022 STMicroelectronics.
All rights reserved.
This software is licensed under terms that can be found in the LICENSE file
